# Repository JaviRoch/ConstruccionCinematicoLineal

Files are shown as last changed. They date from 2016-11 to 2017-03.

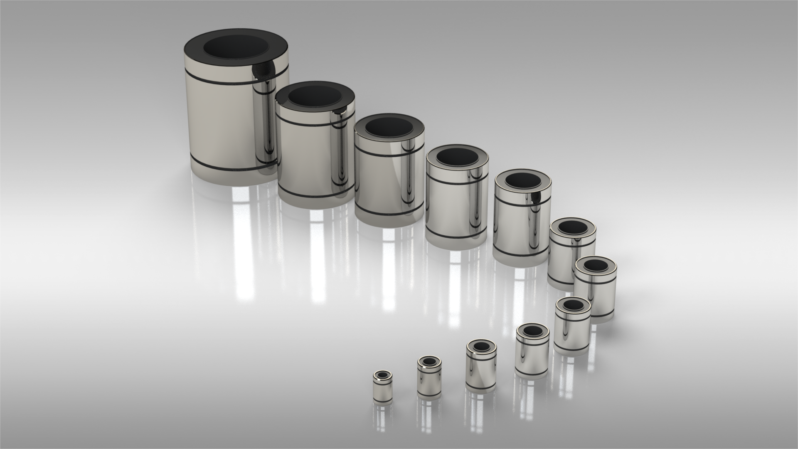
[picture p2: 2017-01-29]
Diseño/Mecánico/Diseño/Solidworks/Eje W/lineare-bearing-lmuu-complete-serie-1.snapshot.3/bearings 2.png

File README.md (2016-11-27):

# Construcción Cinemático Lineal

Proyecto desarrollado dentro de la I Convocatoria [CeSAr-Etopia Labs] (http://cesar-etopia.bifi.es/)

##Descripción

Como fotógrafo parte de mi trabajo se desarrolla en torno a la relación de la arquitectura con la sociedad, investigo y experimento con las formas creadas por los humanos en el paisaje.
Durante el año que pasé en Valencia cursando el master en Fotografía Documental, empecé a interesarme también por la escultura y  comenzó un proceso de autoconocimiento con el que empecé a comprender mi obsesión por las líneas rectas, por la organización, por la unión, por la separación, por el espacio y por el vacío.
Todos estos procesos me hicieron ver que durante muchos años llevaba jugando obsesivamente e inconscientemente con todas las líneas que me rodean. Las junto visualmente, las prolongo con las de otros planos, uno esquinas, las separo equidistantemente…
Es precisamente este juego-obsesión el que quiero representar.
La Construcción Cinemático-Lineal estará compuesta de un obra escultórica sobre la que se proyectarán fotografías y visuales para materializar el juego en una obra artística.

Construcción escultórica:
La construcción tendrá forma de hexaedro con unas medidas de 110x80x50cm e irá instalada sobre pared. En la cara visible frontalmente irá montada una tela elástica.
Bajo esa tela estará el sistema cinemático con la función de crear puntos y aristas empujando la tela.
El sistema cinemático está compuesto de dos cilindros mecánicos, que se desplazarán en el eje Z empujados por unas sirgas accionadas por motores.
Estos cilindros también se desplazarán en el eje X e Y accionados por cuatro pequeños motores, dos para cada eje. 
Entre los dos cilindros habrá un tirante con el que dándole tensión o quitándosela se formará una arista.
El control de secuencia de movimientos se programará en Processing.
El control de movimientos de motores se programará en Arduino.

Proyección:
La proyección que se realizará sobre la construcción estará compuesta de fotografías y de visuales generados con Processing.
Estos estarán relacionados y coordinados con el movimiento de la construcción.

##Pad de comunicación
Este [Pad](https://titanpad.com/gCRByKV6la) se utilizará como herramienta en la que ir anotando idéas, datos o enlaces interesantes para el proyecto.

##Bitácora

Podéis encontrar una bitácora del proceso en la página del autor [Javier Roche](http://javierroche.es/category/cesar/)

##Funcionamiento

Los visuales están programados para funcionar con una pantalla de 1920 x 1080 píxeles. Se podrá ver en pantallas más pequeñas pero se perderá zona de visualización.

###Manual

Se ha programado un modo manual con el que poder realizar movimientos controlados de los motores y visualizar de datos.
Para entrar al modo manual se deberá pulsar la letra 'm'.
En el modo manual se puede avanzar de step con las teclas + y -

##Diagrama de flujo

Diagrama de flujo de flujo no editable, para ver pulsar Sky & Try [Diagrama de flujo](http://flowchart.com/editor/#068e51666a61c3a1:206712)

##Colaboradoras

Daniel Ferrer, María Blasco, José Miguel Cuartero, Fernando Aladrén, Javier Galán

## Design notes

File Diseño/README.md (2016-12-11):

##Mecánico

##Eléctrico

###Componentes

+ 1 Arduino Mega 2560
+ 1 Fuente de alimentación 12V-5V ATX
+ 9 Motores paso a paso NEMA 17  0.34Kg  0.9º por paso
+ 9 Drivers pololu A4988
+ 9 Disipadores 8,5mm para los chips del driver
+ 9 Condensadores 16V 100UF
+ 1 Placa perforada europlaca CI
+ 7 Finales de carrera

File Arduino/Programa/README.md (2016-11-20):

# Programación Arduino 
                                             
 http://cesar-etopia.bifi.es/index.php/2016/10/18/construccion-cinematico-lineal/  
    
  Proyecto CeSAr en etopia        
   Participantes:
    Javier Roche  (lider)   javier.roche.m@gmail.com
    Daniel Ferrer           daniel10_es@yahoo.es
    Jose Miguel Cuartero    crispincuarter@gmail.com
    María Blasco            blascocubas.maria@gmail.com
    ....      

  Agradecimientos a los creadores de la biblioteca TimerOne por su aportación.

  Definición del programa:
    Se basa en la creación de un sistema de 7 ejes coordinados realizado con motores
    paso a paso NEMA17.
    A través de un programa realizado en processing y conectado al ARDUINO MEGA con
    los motores, se coordinarán los 7 ejes con imagenes.
    Para ello, se enviarán los datos de las coordenadas T, U, V, W, X, Y, Z desde un
    programa realizado con processing al arduino para que los motores se posicionen. 
    Una vez que llega a la posición deseada, se informará al programa de processing que ha
    llegado para recibir la siguiente instrucción.
    Durante el trayecto de los ejes, arduino enviará los datos de la posición actual para que
    el programa de processing pueda coordinar con la imagen correspondiente.
    Los ejes tendrán una rutina de inicialización para posicionarse en el (0,0,0,0,0,0,0) la
    cual será llamada desde Processing cuando comience el ciclo.

    Versión: V0.1  Fecha: 20161116

    Velocidad: 9600 baudios.
    Comandos:
      - Modificar posición:
          Tnnn Unnn Vnnn Wnnn Xnnn Ynnn Znnn Fnnn
        Donde:
        T, U, V ... Z son los ejes
        nnn: Es el número del pixel o cota de cada eje donde queremos ir (desde -32768 a 32767
        F: Velocidad del movimiento (desde 0 a 1000)
      - Realizar el origen:
          ORIGEN
        Devuelve un "Origen realizado con exito" cuando lo termina
      - Poner en marcha los motores:
          ON
        Devuelve un "Motores on" cuando termina
      - Apagar los motores:
          OFF
        Devuelve un "Motores off" cuando termina 

    Pendientes de realizar:
      - Rutina origen.
      - Rutina de aceleraciones trapezoidales.
      - Introducir perro guardián de seguridad.
      - Limitar los valores de entrada.
      - Renombrar los ejes correctamente.
      - Comentar el programa.
      - Realizar organigramas explicativos.
      - Terminar biblioteca de textos.

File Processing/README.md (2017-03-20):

##Referencias externas

[Processing] (https://processing.org/)

[Interfaz gráfica de usuario] (http://www.sojamo.de/libraries/controlP5/)

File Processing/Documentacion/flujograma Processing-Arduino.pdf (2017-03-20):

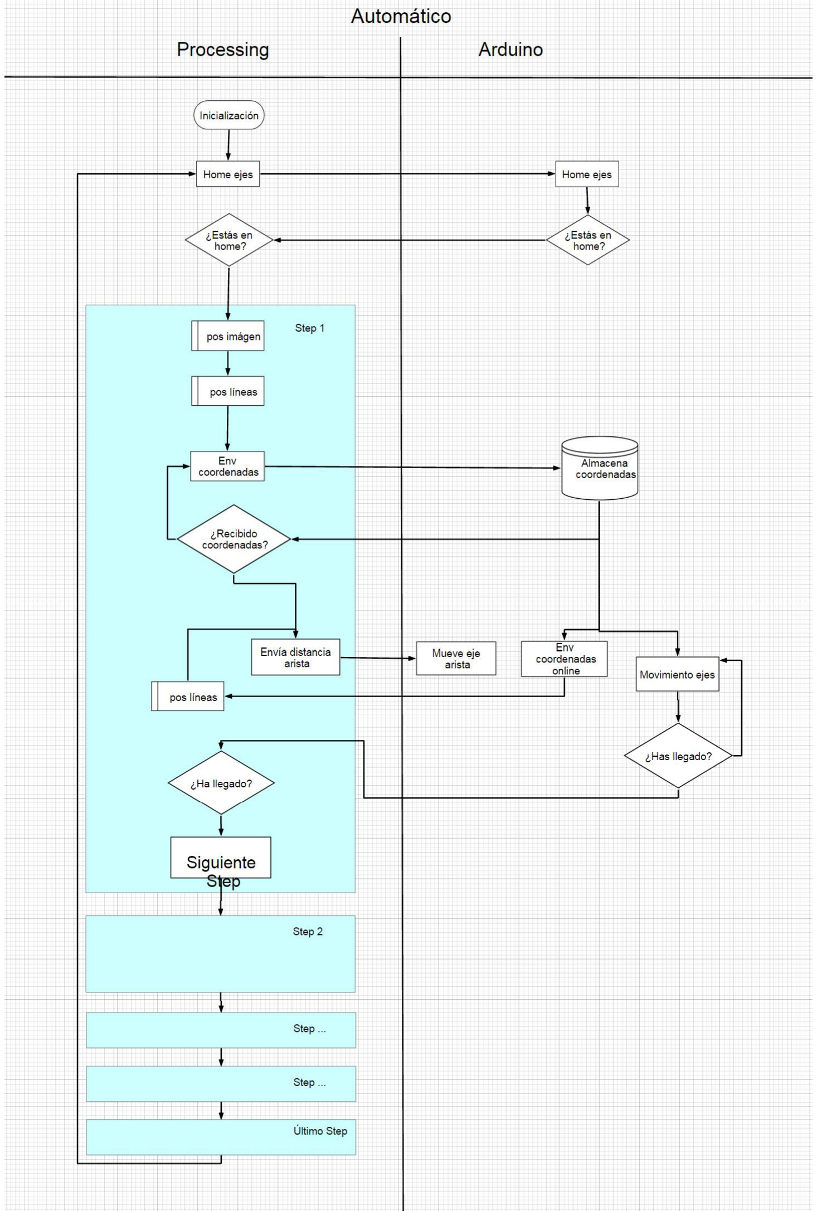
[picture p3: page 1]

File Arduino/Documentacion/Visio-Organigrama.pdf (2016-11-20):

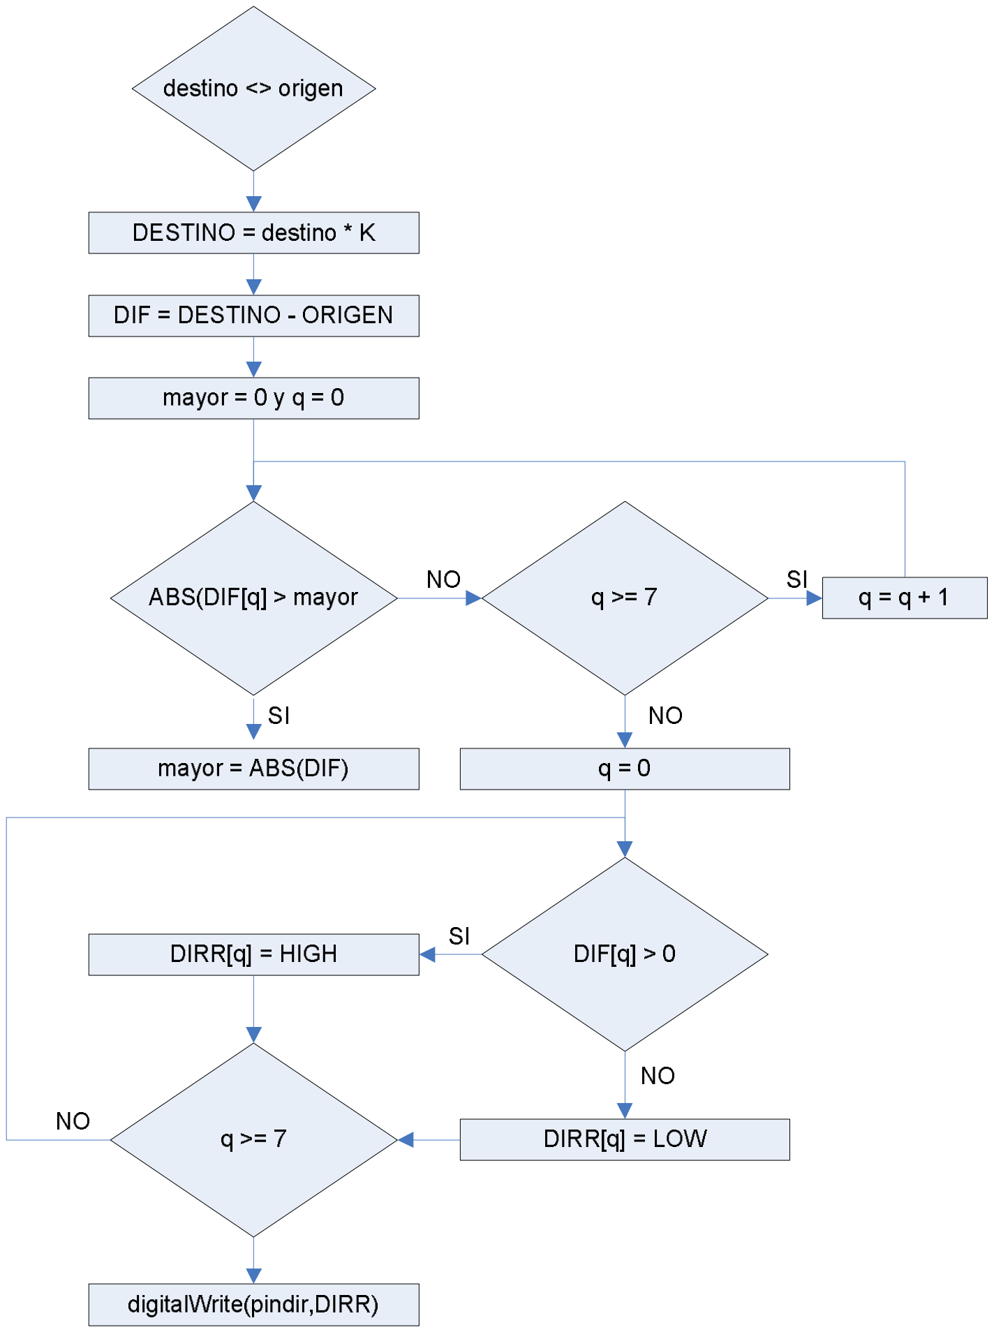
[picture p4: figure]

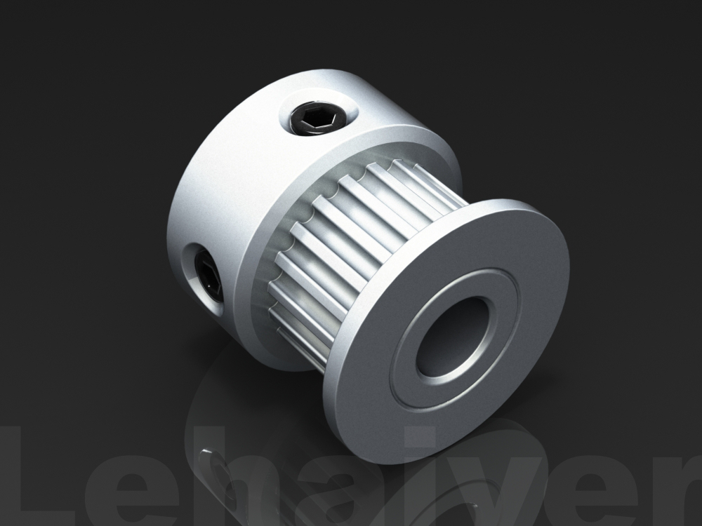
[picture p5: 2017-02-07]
Diseño/Mecánico/Diseño/Solidworks/modificacion/timing-pulley-gt2-20-teeth-5mm-bore-2.snapshot.18/GT2-20T.JPG

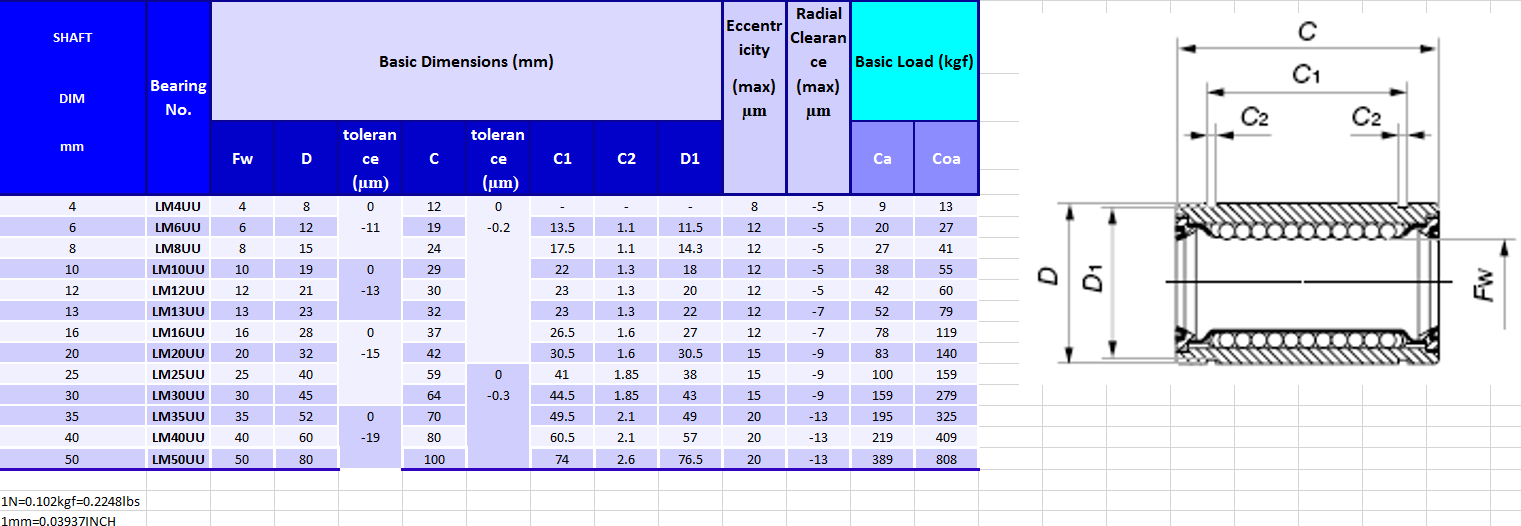
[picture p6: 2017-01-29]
Diseño/Mecánico/Diseño/Solidworks/Eje Z/lineare-bearing-lmuu-complete-serie-1.snapshot.3/bearings overview.png

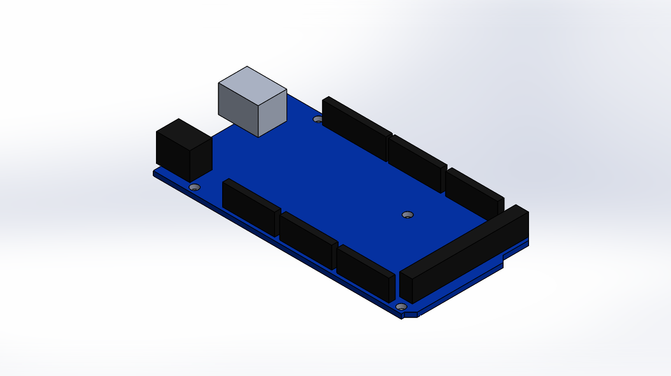
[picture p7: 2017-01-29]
Diseño/Mecánico/Diseño/Solidworks/arduino-mega-r3-1.snapshot.1/Arduino Mega R3.png

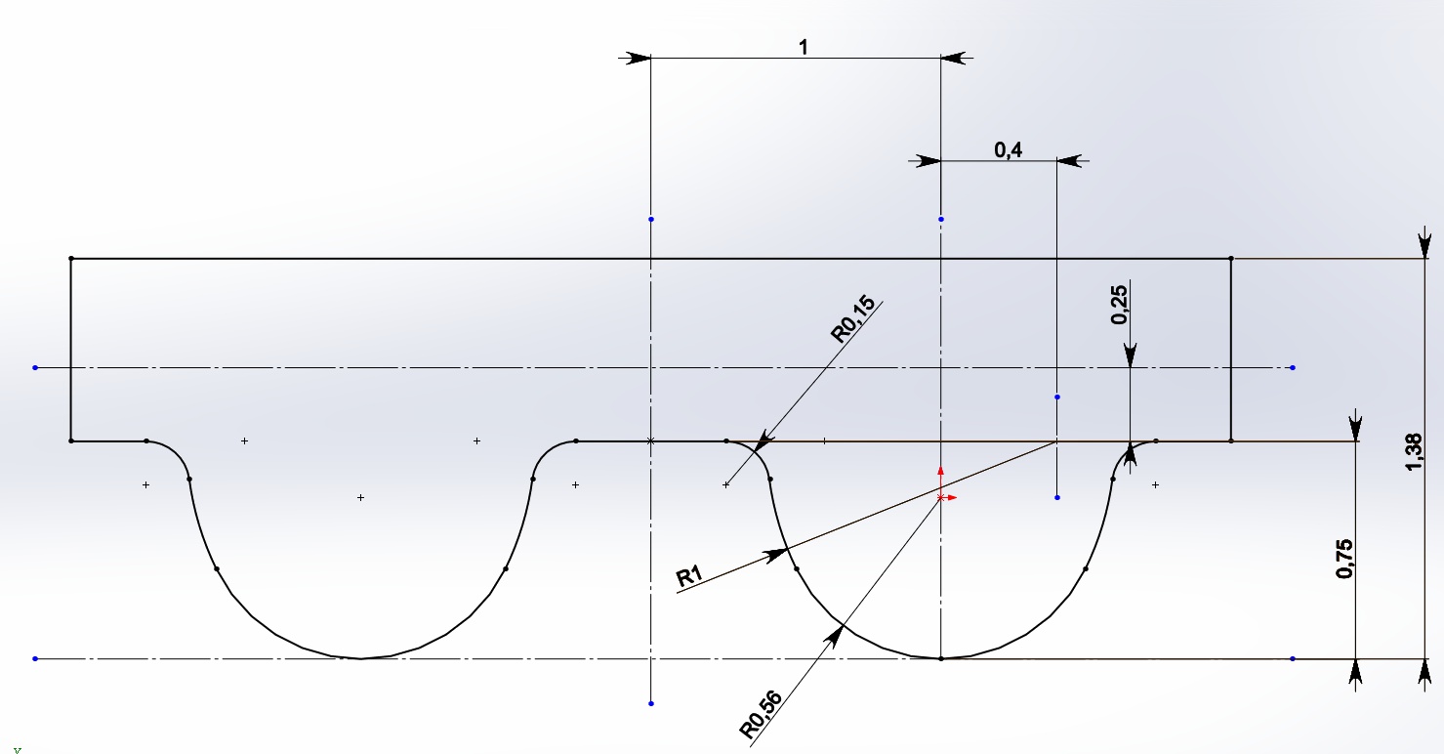
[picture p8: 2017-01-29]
Diseño/Mecánico/Diseño/Solidworks/modificacion/timing-pulley-gt2-20-teeth-5mm-bore-2.snapshot.18/GT2_belt_cut_.JPG

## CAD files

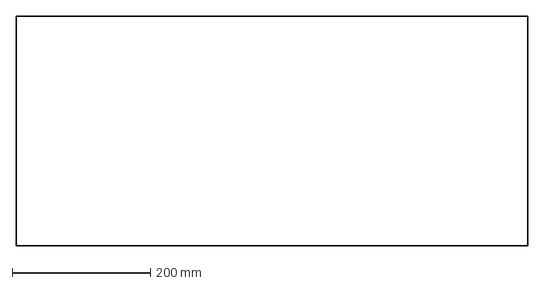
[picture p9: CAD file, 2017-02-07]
Diseño/Mecánico/CNC/Lateral derecho^Ensamblaje_2uni.DXF
740.0 x 332.0 mm

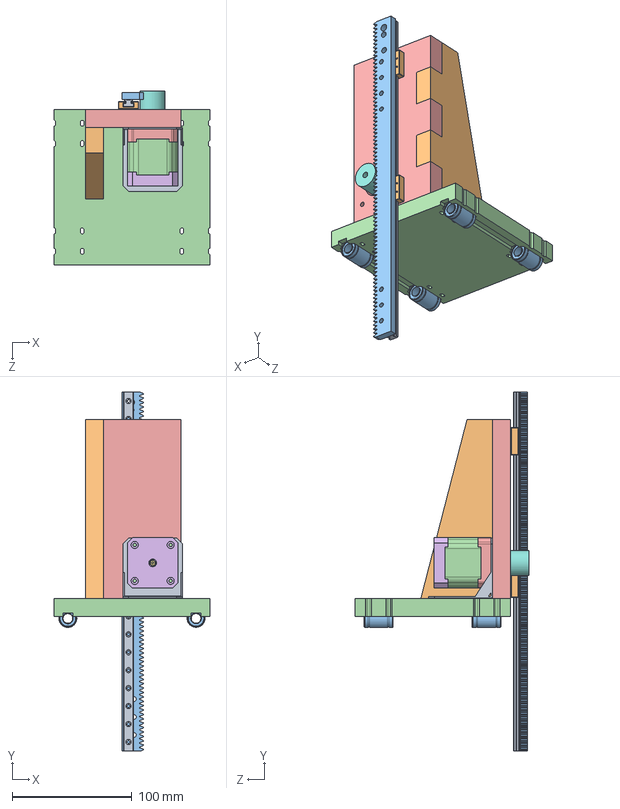
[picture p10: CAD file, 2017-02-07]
Diseño/Mecánico/Diseño/Solidworks/Eje W/Ensamblaje1.SLDASM
130.0 x 300.0 x 145.5 mm
TS_04_07_300_1
TW_04_07_2 x 2
Rack
NEMA 17 Stepper Motor Middle
NEMA 17 Stepper Motor Top
NEMA 17 Stepper Motor Bottom
NEMA 17 Stepper Motor Shaft
polea
nema17_flange_mount
Nervio
Lineare_bearing_LMUU_serie x 4
Base
Copia de Copia de Pieza8^Ensamblaje1

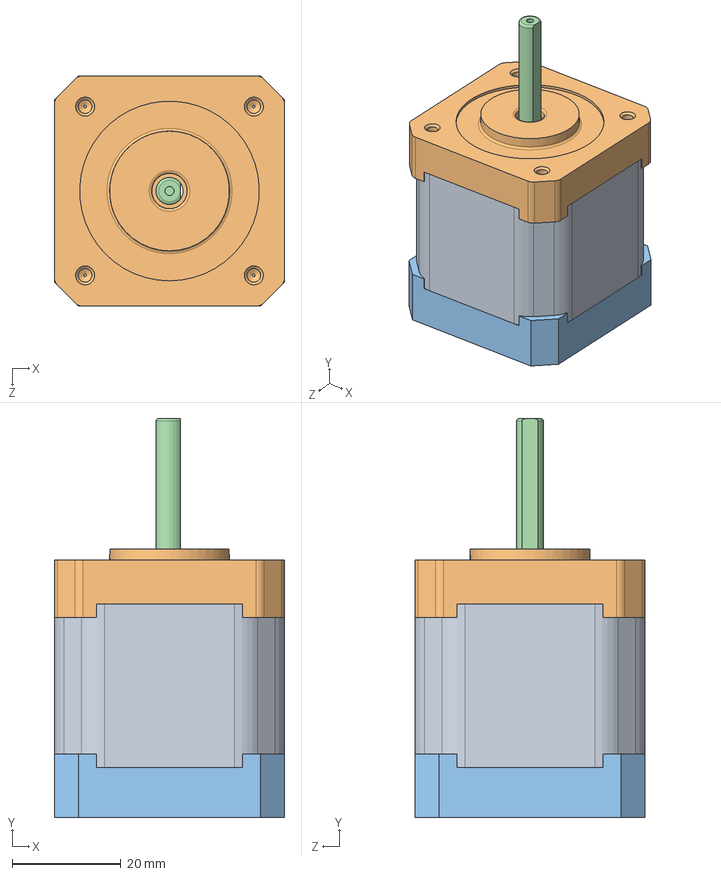
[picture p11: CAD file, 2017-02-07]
Diseño/Mecánico/Diseño/Solidworks/Eje W/nema-17-stepper-motor-1.snapshot.2/NEMA 17 Stepper Motor Assembly.SLDASM
42.3 x 73.3 x 42.3 mm
NEMA 17 Stepper Motor Middle
NEMA 17 Stepper Motor Top
NEMA 17 Stepper Motor Bottom
NEMA 17 Stepper Motor Shaft
pan cross head_am x 4

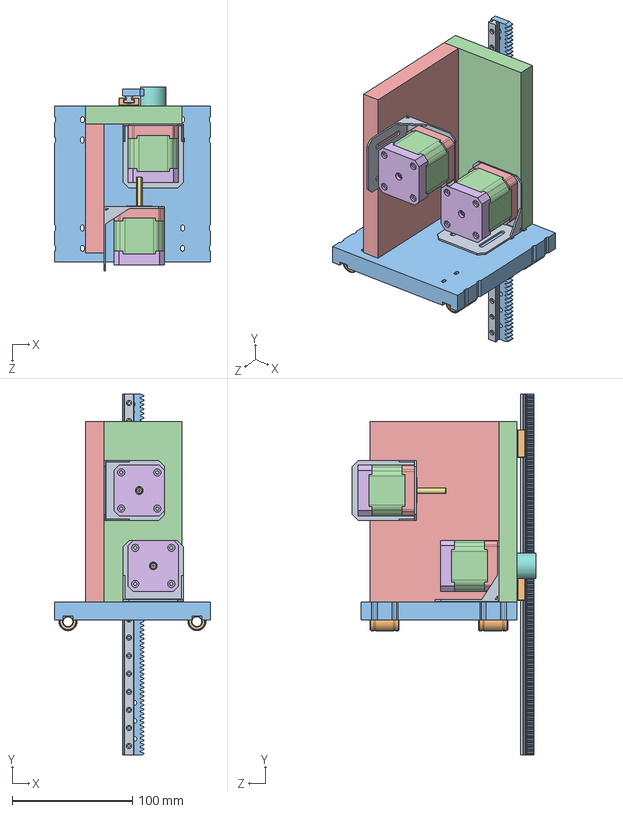
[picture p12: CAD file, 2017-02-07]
Diseño/Mecánico/Diseño/Solidworks/Eje Z/Ensamblaje4z.SLDASM
130.0 x 300.0 x 152.6 mm
TS_04_07_300_1
TW_04_07_2 x 2
Rack
NEMA 17 Stepper Motor Middle x 2
NEMA 17 Stepper Motor Top x 2
NEMA 17 Stepper Motor Bottom x 2
NEMA 17 Stepper Motor Shaft x 2
polea
nema17_flange_mount x 2
Lineare_bearing_LMUU_serie x 4
Base
Copia de Copia de Pieza8^Ensamblaje4z
Pieza1^Ensamblaje4z

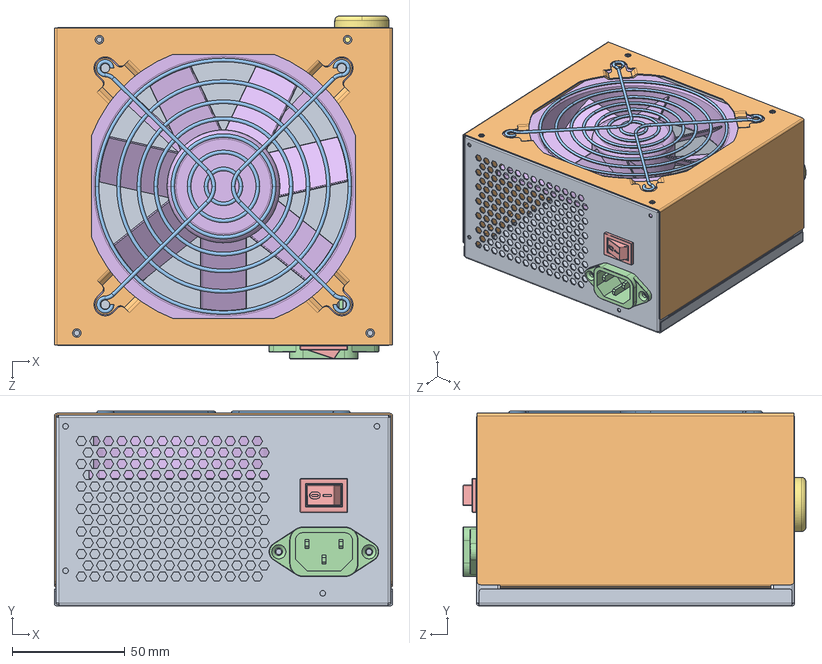
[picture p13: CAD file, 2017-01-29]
Diseño/Mecánico/Diseño/Solidworks/ATX/ATX Power Supply v1.0.SLDASM
150.0 x 86.4 x 152.0 mm
Box v1.0 - ATX Power Supply
Cover v1.0 - ATX Power Supply
Grelha Prot Vent 120
IEC Plug
Switch on-off
Ventax 119x119x26
Casq

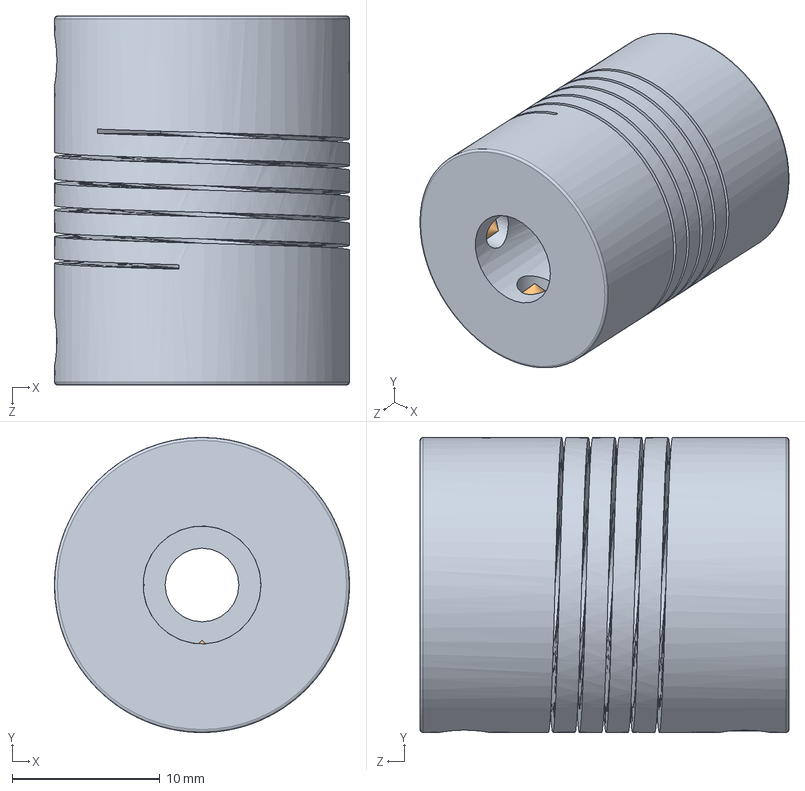
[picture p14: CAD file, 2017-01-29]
Diseño/Mecánico/Diseño/Solidworks/flexible-shaft-coupler-5mm-to-8mm.snapshot.3/Acople Flexible.SLDASM
20.0 x 20.0 x 25.0 mm
Acople FlexibleSLDPRT
socket set screw cone point_am x 4

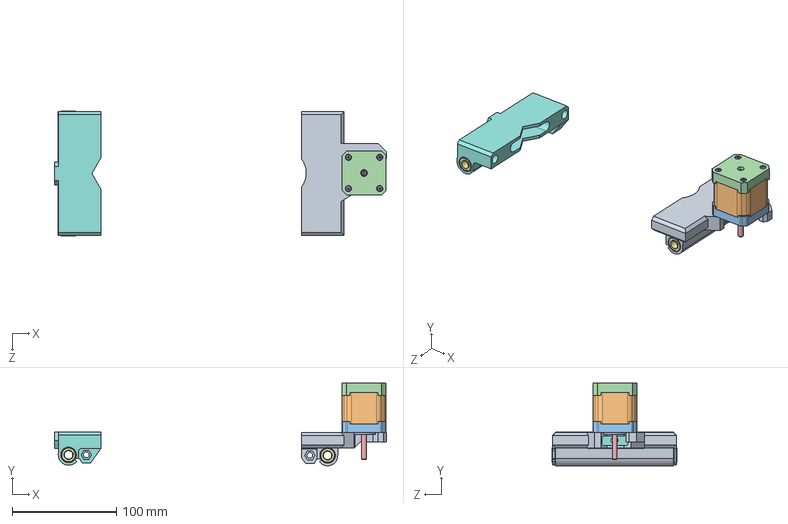
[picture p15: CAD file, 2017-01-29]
Diseño/Mecánico/Diseño/Solidworks/Eje V/Ensamblaje2.SLDASM
318.4 x 79.3 x 120.0 mm
carro_izquierda
NEMA 17 Stepper Motor Middle
NEMA 17 Stepper Motor Top
NEMA 17 Stepper Motor Bottom
NEMA 17 Stepper Motor Shaft
pan cross head_am x 4
Lineare_bearing_LMUU_serie x 4
carro_derecha

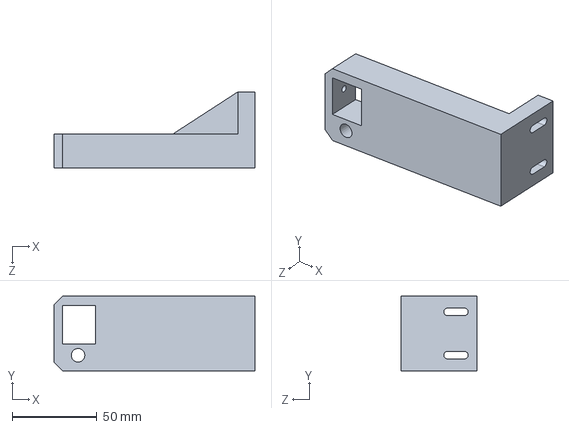
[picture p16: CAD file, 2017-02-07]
Diseño/Mecánico/Diseño/Solidworks/modificacion/soporte_superior_derecho_mod^Ensamblaje.SLDPRT
118.3 x 44.0 x 45.0 mm

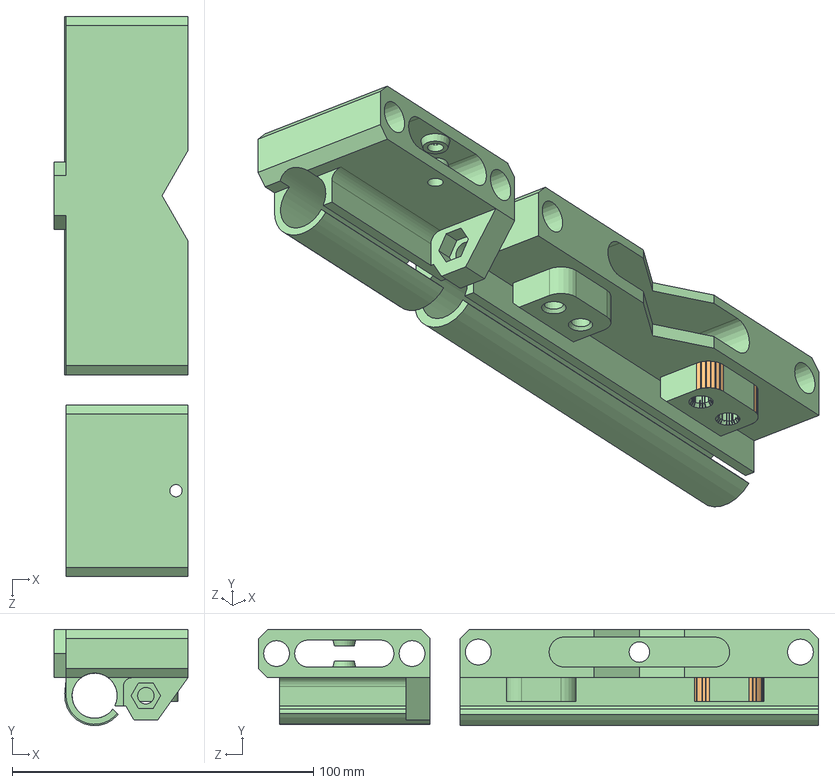
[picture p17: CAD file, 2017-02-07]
Diseño/Mecánico/Diseño/Solidworks/modificacion/carro derecho/Ensamblaje2.SLDASM
44.5 x 31.9 x 186.0 mm
Pieza1^Ensamblaje2
Pieza2^Ensamblaje2

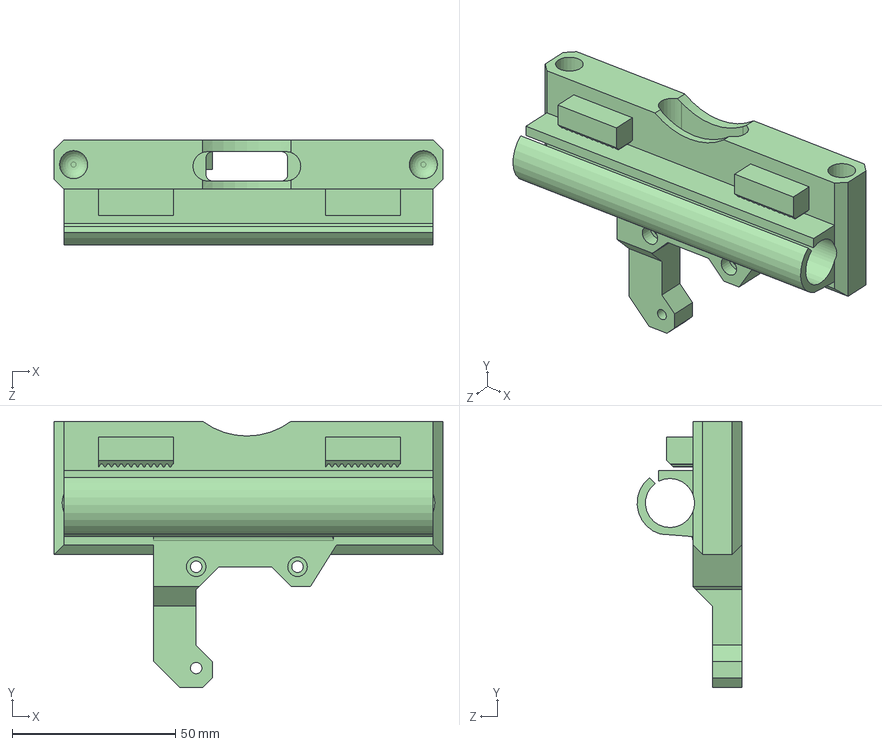
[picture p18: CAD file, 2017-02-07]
Diseño/Mecánico/Diseño/Solidworks/modificacion/carro izquierdo/carro_izquierdo_ensa.SLDASM
119.0 x 81.5 x 32.0 mm

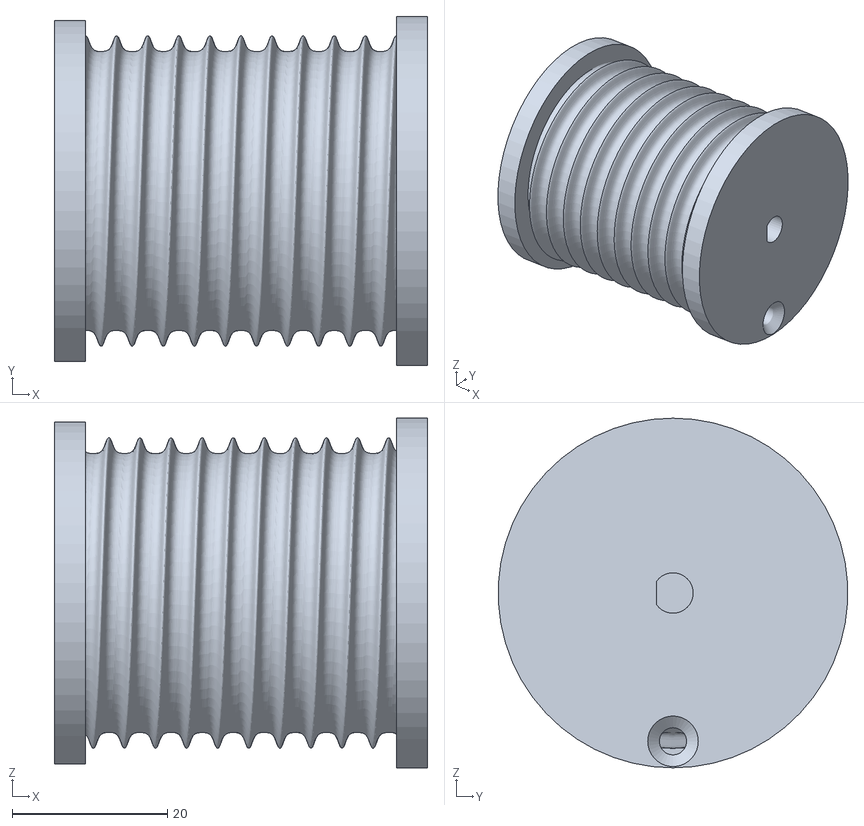
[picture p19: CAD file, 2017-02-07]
Diseño/Mecánico/Impresion 3d/Ensamblaje - Bobina-1.STL
48.0 x 44.9 x 45.0

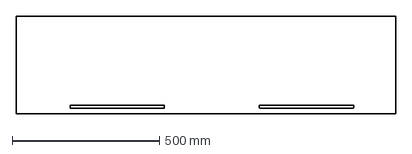
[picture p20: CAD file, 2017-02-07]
Diseño/Mecánico/CNC/Lateral superior^Ensamblaje.DXF
1288.0 x 332.0 mm

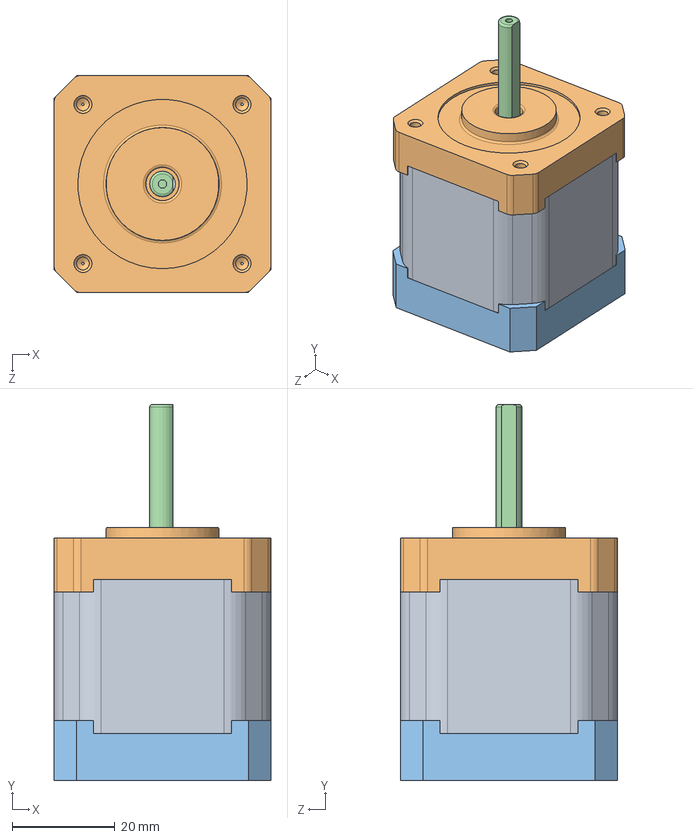
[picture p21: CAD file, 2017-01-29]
Diseño/Mecánico/Diseño/Solidworks/Eje Z/nema-17-stepper-motor-1.snapshot.2/NEMA 17 Stepper Motor Assembly.SLDASM
42.3 x 73.3 x 42.3 mm
NEMA 17 Stepper Motor Middle
NEMA 17 Stepper Motor Top
NEMA 17 Stepper Motor Bottom
NEMA 17 Stepper Motor Shaft

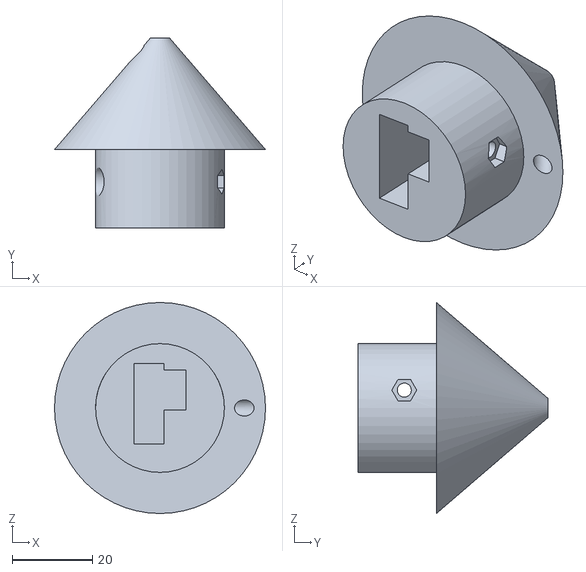
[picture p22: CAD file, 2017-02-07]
Diseño/Mecánico/Impresion 3d/Ensamblaje - Pivote-2.STL
52.4 x 47.2 x 52.4

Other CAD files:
Diseño/Mecánico/Diseño/Solidworks/modificacion/carro derecho/Ensamblaje1.SLDASM
Diseño/Mecánico/Impresion 3d/soporte_superior_derecho_mod^Ensamblaje.STL
Diseño/Mecánico/Impresion 3d/soporte_superior_izquierdo_mod^Ensamblaje.STL
Diseño/Mecánico/Impresion 3d/Ensamblaje - Polea_grande.STL
Diseño/Mecánico/CNC/Base_chasis.DXF
Diseño/Mecánico/CNC/Base_eje_horizontal_mod_2uni.DXF
Diseño/Mecánico/CNC/Guia_cuerda.DXF
Diseño/Mecánico/CNC/Lateral inferior^Ensamblaje.DXF
Diseño/Mecánico/CNC/Lateral_eje_con_tolerancias.DXF
Diseño/Mecánico/CNC/Lateral_eje_con_tolerancias2.DXF
Diseño/Mecánico/CNC/Lateral_eje_con_tolerancias3.DXF
Diseño/Mecánico/CNC/Nervio_con_tolerancias.DXF
Diseño/Mecánico/CNC/Nervio_con_tolerancias2.DXF
Diseño/Mecánico/CNC/Pared_motor_con_tolerancias2_2uni.DXF
Diseño/Mecánico/CNC/Pared_motor_con_tolerancias_2uni.DXF
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

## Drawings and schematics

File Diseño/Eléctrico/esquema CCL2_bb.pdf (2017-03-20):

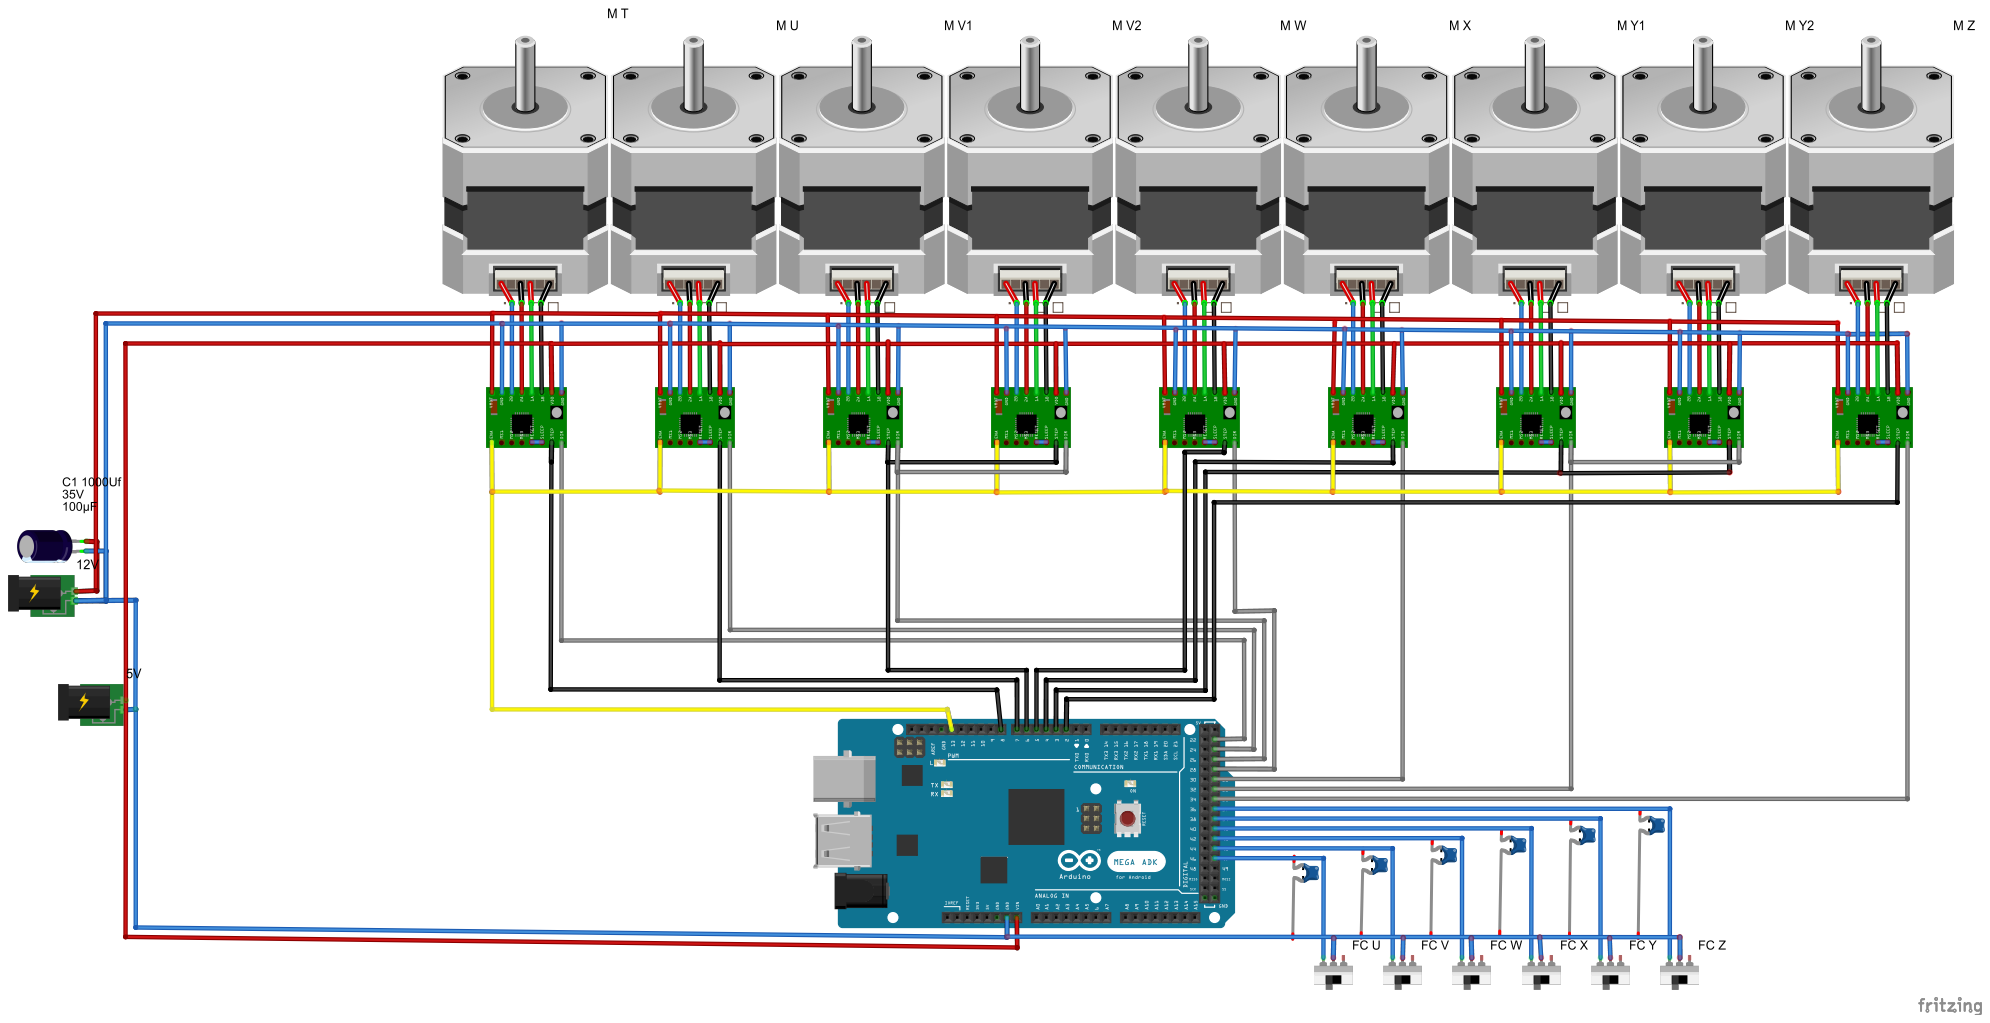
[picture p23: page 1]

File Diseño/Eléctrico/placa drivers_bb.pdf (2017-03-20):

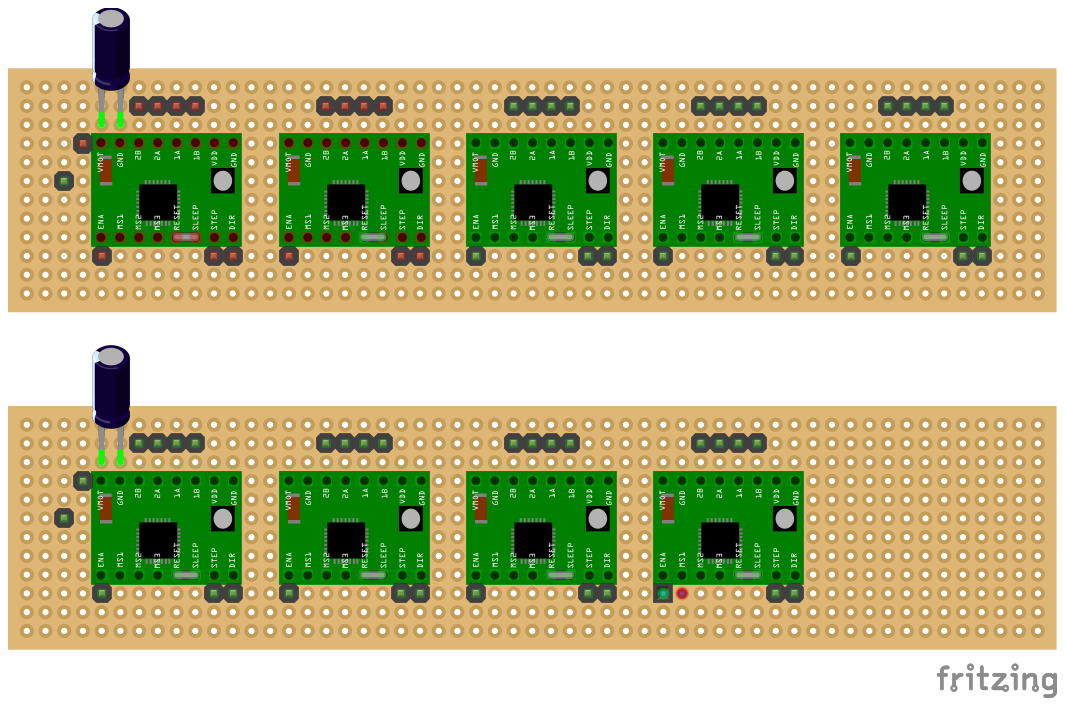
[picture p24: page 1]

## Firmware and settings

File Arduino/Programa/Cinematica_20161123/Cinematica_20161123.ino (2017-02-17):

/*---------------------------------------------------------------------------------------------
                       Construcción Cinemático-Lineal           
                                             
 http://cesar-etopia.bifi.es/index.php/2016/10/18/construccion-cinematico-lineal/  
    
  Proyecto CeSAr en etopia        
   Participantes:
    Javier Roche  (lider)   javier.roche.m@gmail.com
    Daniel Ferrer           daniel10_es@yahoo.es
    Jose Miguel Cuartero    crispincuarter@gmail.com
    María Blasco            blascocubas.maria@gmail.com
    ....      

  Agradecimientos a los creadores de la biblioteca TimerOne por su aportación.

  Definición del programa:
    Se basa en la creación de un sistema de 7 ejes coordinados realizado con motores
    paso a paso NEMA17.
    A través de un programa realizado en processing y conectado al ARDUINO MEGA con
    los motores, se coordinarán los 7 ejes con imagenes.
    Para ello, se enviarán los datos de las coordenadas T, U, V, W, X, Y, Z desde un
    programa realizado con processing al arduino para que los motores se posicionen. 
    Una vez que llega a la posición deseada, se informará al programa de processing que ha
    llegado para recibir la siguiente instrucción.
    Durante el trayecto de los ejes, arduino enviará los datos de la posición actual para que
    el programa de processing pueda coordinar con la imagen correspondiente.
    Los ejes tendrán una rutina de inicialización para posicionarse en el (0,0,0,0,0,0,0) la
    cual será llamada desde Processing cuando comience el ciclo.

    Versión: V0.3  Fecha: 20161123

    Velocidad: 57600 baudios.
    Comandos:
      - Modificar posición:
          Tnnn Unnn Vnnn Wnnn Xnnn Ynnn Znnn Fnnn
        Donde:
        T, U, V ... Z son los ejes
        nnn: Es el número del pixel o cota de cada eje donde queremos ir (desde -32768 a 32767
        F: Velocidad del movimiento (desde 0 a 1000)
      - Realizar el origen:
          ORIGEN
        Devuelve un "Origen realizado con exito" cuando lo termina
      - Poner en marcha los motores:
          ON
        Devuelve un "Motores on" cuando termina
      - Apagar los motores:
          DES
        Devuelve un "Motores off" cuando termina 

    Pendientes de realizar:
      - Introducir perro guardián de seguridad.
      - Limitar los valores de entrada.
      - Comentar el programa en detalle.
      - Realizar organigramas explicativos.
------------------------------------------------------------------------------------------------*/

/* LIBRERIAS */
#include "pins.h"
#include "textos.h"
#include "inicializacion.h"
#include "TimerOne.h"

#define acc 50

/*VARIABLES GLOBALES*/
byte indice = 0;    /*Indice de la cadena de datos que se envia desde processing*/

char COMANDOS[80];  /*Cadena de caracteres que processing envia en forma de comandos*/
char arg[8] = {'T','U','V','W','X','Y','Z','F'};      /*Ejes y velocidad*/

int destino[8];           // T, U, V, W, X, Y, Z, F   Donde queremos ir (comando de processing) en pixeles
int origen[8];            // T, U, V, W, X, Y, Z, F   De donde venimos en pixeles
int posicion[8];          // T, U, V, W, X, Y, Z, F   Donde estamos actualmente (para enviar a processing)
int posicion_anterior[8]; // T, U, V, W, X, Y, Z, F   Auxiliar para saber si se ha cambiado la posición
int velocidad_anterior;   // Auxiliar

float K[8] = {10,10,10,10,10,10,10,1};  //Factor que relaciona los pixeles con los pasos (pixeles x pasos)
float DESTINO[8];                       // T, U, V, W, X, Y, Z, F Donde queremos ir (comando de processing) en pasos
float ORIGEN[8];                        // T, U, V, W, X, Y, Z, F Auxiliar para saber que vamos a cambiar de cota en pasos
float POSICION[8];                      // T, U, V, W, X, Y, Z, F Donde estamos actualmente (para enviar a processing) en pasos
float FAC[7];                           // T, U, V, W, X, Y, Z, Factores de linealización de los pasos cuando se sincronizan
float DIF[8];                           // Diferencia en pasos de los ejes 
float mayor = 0;  //Mayor diferencia de pasos del eje que más pasos tiene que dar para llegar a la cota establecida

long REC[7];                            // Auxiliar

int STEPS[7]    = {T_STEP_PIN,   U_STEP_PIN,   V_STEP_PIN,   W_STEP_PIN,   X_STEP_PIN,   Y_STEP_PIN,   Z_STEP_PIN   };
int ENABLE[7]   = {T_ENABLE_PIN, U_ENABLE_PIN, V_ENABLE_PIN, W_ENABLE_PIN, X_ENABLE_PIN, Y_ENABLE_PIN, Z_ENABLE_PIN };
int DIR_PIN[7]  = {T_DIR_PIN,    U_DIR_PIN,    V_DIR_PIN,    W_DIR_PIN,    X_DIR_PIN,    Y_DIR_PIN,    Z_DIR_PIN    };
int MIN_PIN[7]  = {T_MIN_PIN,    U_MIN_PIN,    V_MIN_PIN,    W_MIN_PIN,    X_MIN_PIN,    Y_MIN_PIN,    Z_MIN_PIN    };

bool DIRR[8];                 // Dirección de los motores
bool PETICION_ORIGEN = LOW;   // Flag petición para realizar el origen
bool OOK[7];                  // Origen realizado de cada eje

bool busy = LOW;
bool motores_on = LOW;
bool FL1 = LOW;
bool FL2 = LOW;
bool ook;

long t_ant;
long t_ant2;
int v;
float aux;
float aux2;
 

void setup() {
  inicializacion();
  Timer1.initialize(2000); 
  Timer1.attachInterrupt(trazar); 
  destino[7] = 800;
  for (int q = 0; q < 7; q++) {
    OOK[q] = LOW;
  }  
  Serial.println(MSG_ARRANQUE);
}

void trazar() {   /* Función crítica, lo más rápida posible*/
  if (busy == HIGH) {
    if (mayor > 0) {
      for (int q = 0; q < 7; q++) {
        long a = ceil(mayor*FAC[q]);
        if (a != REC[q]) {
          digitalWrite(STEPS[q], HIGH);   /* Flanco del paso */
          digitalWrite(STEPS[q], LOW);    /* Flanco del paso */
          if (DIRR[q] == HIGH) {
            POSICION[q]++;
          } else {
            POSICION[q]--;
          }
          REC[q] = a;   
        }     
      }
      mayor--; 
    } else {
      busy = LOW;
    }
  }
}

void marcha() { /* Activa los motores */
  for (int q = 0; q < 7; q++) { 
    digitalWrite(ENABLE[q], LOW);
  }
}

void paro() {  /* Desactiva los motores */
  for (int q = 0; q < 7; q++) { 
    digitalWrite(ENABLE[q], HIGH);
  }  
}

void origen_coordenadas() {  /* Realiza el origen de coordenadas */
  destino[7] = 800;

  /*Origen eje T*/
  if (OOK[0] == LOW) {
    destino[0] = -10000;  
    if (digitalRead(MIN_PIN[0]) == LOW) {
      destino[0] = 0;
      origen[0] = 0;
      posicion[0] = 0;
      POSICION[0] = 0;
      mayor = 0;
      posicion_anterior[0] = 0;
      OOK[0] = HIGH;
    } 
  }

  /*Origen eje U*/
  if (OOK[1] == LOW && OOK[0] == HIGH) {
    destino[1] = -10000; 
    if (digitalRead(MIN_PIN[1]) == LOW) {
      destino[1] = 0;
      origen[1] = 0;
      posicion[1] = 0;
      POSICION[1] = 0;
      mayor = 0;
      posicion_anterior[1] = 0;
      OOK[1] = HIGH;
    }  
  }

  /*Origen eje V*/
  if (OOK[2] == LOW && OOK[1] == HIGH && OOK[0] == HIGH) {
    destino[2] = -10000;  
    if (digitalRead(MIN_PIN[2]) == LOW) {
      destino[2] = 0;
      origen[2] = 0;
      posicion[2] = 0;
      POSICION[2] = 0;
      mayor = 0;
      posicion_anterior[2] = 0;
      OOK[2] = HIGH;
    }  
  }

  /*Origen eje W*/
  if (OOK[3] == LOW && OOK[2] == HIGH && OOK[1] == HIGH  && OOK[0] == HIGH) {
    destino[3] = -10000; 
    if (digitalRead(MIN_PIN[3]) == LOW) {
      destino[3] = 0;
      origen[3] = 0;
      posicion[3] = 0;
      POSICION[3] = 0;
      mayor = 0;
      posicion_anterior[3] = 0;
      OOK[3] = HIGH;
    } 
  }

  /*Origen eje X*/
  if (OOK[4] == LOW && OOK[3] == HIGH && OOK[2] == HIGH  && OOK[1] == HIGH && OOK[0] == HIGH) {
    destino[4] = -10000; 
    if (digitalRead(MIN_PIN[4]) == LOW) {
      destino[4] = 0;
      origen[4] = 0;
      posicion[4] = 0;
      POSICION[4] = 0;
      mayor = 0;
      posicion_anterior[4] = 0;
      OOK[4] = HIGH;
    }  
  }

  /*Origen eje Y*/
  if (OOK[5] == LOW && OOK[4] == HIGH && OOK[3] == HIGH  && OOK[2] == HIGH && OOK[1] == HIGH && OOK[0] == HIGH) {
    destino[5] = -10000;  
    if (digitalRead(MIN_PIN[5]) == LOW) {
      destino[5] = 0;
      origen[5] = 0;
      posicion[5] = 0;
      POSICION[5] = 0;
      mayor = 0;
      posicion_anterior[5] = 0;
      OOK[5] = HIGH;
    }
  }

  /*Origen eje Z*/
  if (OOK[6] == LOW && OOK[5] == HIGH && OOK[4] == HIGH  && OOK[3] == HIGH && OOK[2] == HIGH && OOK[1] == HIGH  && OOK[0] == HIGH) {
    destino[6] = -100; 
    if (digitalRead(MIN_PIN[6]) == LOW) {
      destino[6] = 0;
      origen[6] = 0;
      posicion[6] = 0;
      POSICION[6] = 0;
      mayor = 0;
      posicion_anterior[6] = 0;
      OOK[6] = HIGH;
    } 
  }
  
  /*Reset petición de origen*/
  if (OOK[6] == HIGH && OOK[5] == HIGH && OOK[4] == HIGH  && OOK[3] == HIGH && OOK[2] == HIGH && OOK[1] == HIGH  && OOK[0] == HIGH) {
    PETICION_ORIGEN = LOW;
  }
}

void calcular() {    /* Calculo de pasos */
  
  for (int q = 0; q < 7; q++) { 
    DESTINO[q] = destino[q] * K[q];  /*Calculo del destino en pasos*/
    DIF[q] = DESTINO[q] - ORIGEN[q]; /*Calculo del diferencial en pasos*/
  }

  /*Calculo del mayor*/
  mayor = 0;
  for (int q = 0; q < 7; q++) {
    if (abs(DIF[q])>mayor){
      mayor = abs(DIF[q]);
    }
  }

  /*Calculo de la dirección*/
  for (int q = 0; q < 7; q++) {
    if (DIF[q]>0.0){
      DIRR[q] = HIGH;
    } else {
      DIRR[q] = LOW;
    }
  }

  /*Establece la dirección de los motores*/
  for (int q = 0; q < 7; q++) {
    digitalWrite(DIR_PIN[q],DIRR[q]);
  }

  /*Calculo de los factores*/
  for (int q = 0; q < 7; q++) {
    FAC[q] = abs(DIF[q])/mayor;
  }
}

/* Analizar los comandos enviados desde processing */
void parsear (String trama){
  int i = 0;
  int fin = 0;
  for (int q = 0; q < 8; q++) {                       //Interrogamos los 7 ejes
    if (trama.indexOf(arg[q],0) >= 0) {               //Si existe la letra como argumento
      i = trama.indexOf(arg[q],0);                    //Nos posicionamos en ella
      fin = trama.indexOf(' ',i);                     //Calculamos el tamaño del numero
      destino[q] = trama.substring(i+1,fin).toInt();  //Creamos la cadena de texto y la pasamos a entero
    }
  }

  /* Realizar origen */
  if (trama == "ORIGEN") {
    PETICION_ORIGEN = HIGH;
    for (int q = 0; q < 7; q++) {
      OOK[q] = LOW;
    }  
  }

/* Encender motores */
  if (trama == "ON") {
    marcha();
    Serial.println(MSG_MOTORES_ON);
    motores_on = HIGH;
  }

/* Apagar motores */
  if (trama == "DES") {
    paro();
    Serial.println(MSG_MOTORES_OFF);
    motores_on = LOW;
  }
}

void loop() {
  /* Leer los comandos de processing */
  while (Serial.available() > 0) {
    char caracter = Serial.read();
    if(caracter == '\r') {
      /* El comando ha sido leido. Es hora de analizarlo */
      parsear(COMANDOS);
      indice = 0;
      COMANDOS[indice] = NULL;
    } else {
      COMANDOS[indice] = caracter;
      indice++;
      COMANDOS[indice] = '\0'; //Mantiene el caracter NULL al final de la cadena
    }
  }

/* Realizar origen */
  if (PETICION_ORIGEN == HIGH) {
    origen_coordenadas();
  }

/* Mensaje de destino alcanzado*/
  if (busy == HIGH && FL1 == LOW) {
    FL1 = HIGH;
    aux = mayor;
  }

  if (busy == LOW) {
    FL1 = LOW;
  }

/* Mensaje de destino alcanzado*/
  if (busy == LOW && FL2 == LOW) {
    FL2 = HIGH;
    Serial.println(MSG_TARGET);
  }

  if (busy == HIGH) {
    FL2 = LOW;
  }

/*-----------------------------------------------------------------------------------------------------*/
/* Aceleración */
  if((busy == HIGH) && (millis() > (t_ant + 50)) && (mayor > aux2)) {
    if (v < destino[7]) {
      if ((v + acc) < destino[7]) {v = v + acc;} else {v = destino[7]; aux2 = aux - mayor; }
    } 
    
    t_ant = millis();
    int a = map(v,0,1000,30000,1000);
    Timer1.initialize(a);
  }

  /* Deceleración */
  if((busy == HIGH) && (millis() > (t_ant2 + 50)) && (mayor < aux2)) {
    v = v - acc;
    t_ant2 = millis();
    int a = map(v,0,1000,30000,1000);
    Timer1.initialize(a);
  }

  if (busy == LOW) {
    v = 0;
    aux = 0;
  }
  /*-------------------------------------------------------------------------------------*/

  if ((destino[7]==velocidad_anterior)==LOW) {
    velocidad_anterior=destino[7];
    POSICION[7] = destino[7];
  }

/* Controla si ha cambiado el valor de algún eje*/
  if ((destino[0]==origen[0] && 
       destino[1]==origen[1] &&
       destino[2]==origen[2] && 
       destino[3]==origen[3] && 
       destino[4]==origen[4] && 
       destino[5]==origen[5] && 
       destino[6]==origen[6]) == LOW) {
    busy = LOW;
    for (int q = 0; q < 7; q++) {
      origen[q] = destino[q];
      ORIGEN[q] = POSICION[q];
    }  
    calcular(); 
    Serial.println(MSG_OK);
    busy = HIGH; //Llamamos a la función que recalcula los datos
  }

/* Refrescamos la posición actual */
  for (int q = 0; q < 8; q++) {
    posicion[q] = long(ceil(POSICION[q]/K[q]));  //Recalculamos la posición actual
  } 

/* Respuesta de Arduino a processing de la posición y la velocidad actual*/
  if ((posicion[0]==posicion_anterior[0] && 
       posicion[1]==posicion_anterior[1] && 
       posicion[2]==posicion_anterior[2] && 
       posicion[3]==posicion_anterior[3] && 
       posicion[4]==posicion_anterior[4] && 
       posicion[5]==posicion_anterior[5] && 
       posicion[6]==posicion_anterior[6]) == LOW) {
    for (int q = 0; q < 8; q++) {
      Serial.print(arg[q]);
      Serial.print(posicion[q]);
      Serial.print(" ");
      posicion_anterior[q] = posicion[q];
    }
    Serial.println(" "); 
  }
}

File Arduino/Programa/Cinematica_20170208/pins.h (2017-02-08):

/* Define aqui los pines del Arduino Mega */
/* Los pines desde el 54 al 69 son las analógicas usadas como digitales */

/* Eje T */
#define T_STEP_PIN         8
#define T_DIR_PIN          23
#define T_ENABLE_PIN       13
#define T_MIN_PIN          49
#define T_MAX_PIN          -1

/* Eje U */
#define U_STEP_PIN         7
#define U_DIR_PIN          25
#define U_ENABLE_PIN       13
#define U_MIN_PIN          47
#define U_MAX_PIN          -1

/* Eje V */
#define V_STEP_PIN         6
#define V_DIR_PIN          27
#define V_ENABLE_PIN       13
#define V_MIN_PIN          45
#define V_MAX_PIN          -1

/* Eje W */
#define W_STEP_PIN         5
#define W_DIR_PIN          29
#define W_ENABLE_PIN       13
#define W_MIN_PIN          43
#define W_MAX_PIN          -1

/* Eje X */
#define X_STEP_PIN         4
#define X_DIR_PIN          31
#define X_ENABLE_PIN       13
#define X_MIN_PIN          41
#define X_MAX_PIN          -1

/* Eje Y */
#define Y_STEP_PIN         3
#define Y_DIR_PIN          33
#define Y_ENABLE_PIN       13
#define Y_MIN_PIN          39
#define Y_MAX_PIN          -1

/* Eje Z */
#define Z_STEP_PIN         2
#define Z_DIR_PIN          35
#define Z_ENABLE_PIN       13
#define Z_MIN_PIN          37
#define Z_MAX_PIN          -1

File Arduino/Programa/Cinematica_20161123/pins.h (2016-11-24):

/* Define aqui los pines del Arduino Mega */
/* Los pines desde el 54 al 69 son las analógicas usadas como digitales */

/* Eje T */
#define T_STEP_PIN         54
#define T_DIR_PIN          55
#define T_ENABLE_PIN       38
#define T_MIN_PIN           3
#define T_MAX_PIN          -1

/* Eje U */
#define U_STEP_PIN         60
#define U_DIR_PIN          61
#define U_ENABLE_PIN       56
#define U_MIN_PIN           2
#define U_MAX_PIN          -1

/* Eje V */
#define V_STEP_PIN         46
#define V_DIR_PIN          48
#define V_ENABLE_PIN       62
#define V_MIN_PIN          14
#define V_MAX_PIN          -1

/* Eje W */
#define W_STEP_PIN         26
#define W_DIR_PIN          28
#define W_ENABLE_PIN       24
#define W_MIN_PIN          18
#define W_MAX_PIN          -1

/* Eje X */
#define X_STEP_PIN         -1
#define X_DIR_PIN          -1
#define X_ENABLE_PIN       -1
#define X_MIN_PIN          -1
#define X_MAX_PIN          -1

/* Eje Y */
#define Y_STEP_PIN         -1
#define Y_DIR_PIN          -1
#define Y_ENABLE_PIN       -1
#define Y_MIN_PIN          -1
#define Y_MAX_PIN          -1

/* Eje Z */
#define Z_STEP_PIN         -1
#define Z_DIR_PIN          -1
#define Z_ENABLE_PIN       -1
#define Z_MIN_PIN          -1
#define Z_MAX_PIN          -1

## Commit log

2016-11-07 Actualizo denominaciones motores
2016-11-18 Carga programa Arduino
2016-11-22 Se añade el Pad
2016-11-24 Actualización programas
    [EjeX_Polea_rodamientoB623ZZ.stl, EjeX_carro_A.stl, EjeX_derecha.stl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]
2016-11-27 Actualización
    [EjeZ_soporte_inferior_derecha.stl, EjeZ_soporte_inferior_izquierda.stl]
2016-12-11 Actualización diseño
    [Calce inferior.SLDPRT, EjeX_carro_B.stl, EjeZ_soporte_superior1.SLDPRT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]
2017-01-15 eliminar esquemas
    [esquema CCL.fzz, esquema CCL1.fzz]
2017-01-29 diseño 3d
    [ATX Power Supply v1.0.SLDASM, Acople Flexible.SLDASM, Acople FlexibleSLDPRT.SLDPRT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]
2017-02-07 actualizacion diseño 3d
    [ATX Power Supply v1.0.SLDASM, Acople Flexible.SLDASM, Acople FlexibleSLDPRT.SLDPRT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]
2017-02-17 actualiza 3d
    [ATX Power Supply v1.0.SLDASM, Acople Flexible.SLDASM, Acople FlexibleSLDPRT.SLDPRT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]
